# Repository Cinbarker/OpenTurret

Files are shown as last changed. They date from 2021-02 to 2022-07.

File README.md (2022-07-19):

# Open Turret
An open sourced highly accurate pan-tilt system for anything that needs to be panned and tilted!\
My goal for this project is to make a precise pan tilt mechanism that is accessible for everyone.
The hardware is still quite experimental, but I hope to refine it and release build instructions soon. Feel free to
contact me if you are interested in contributing, I will happily provide further build details.

<p float="left">
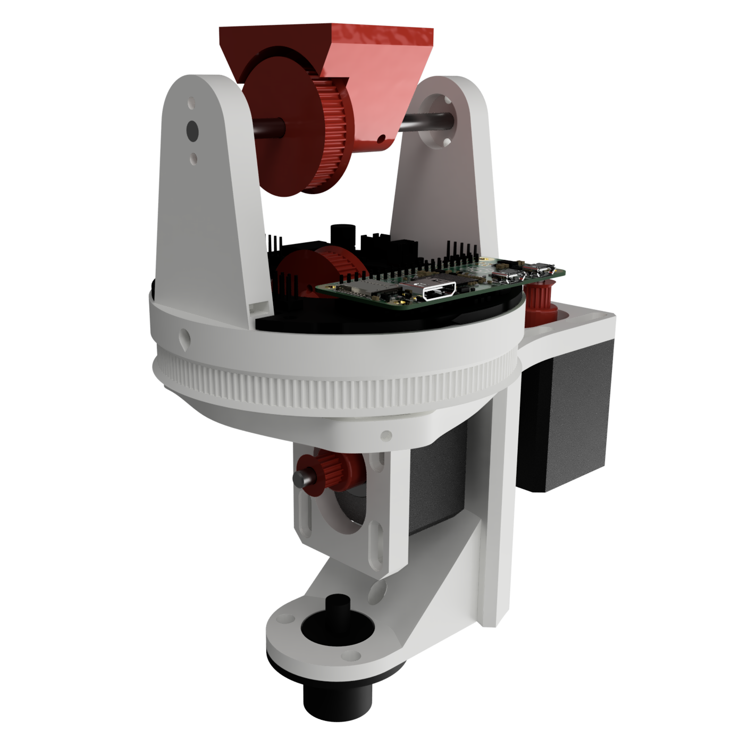
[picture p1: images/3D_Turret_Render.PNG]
3D Turret Render
  
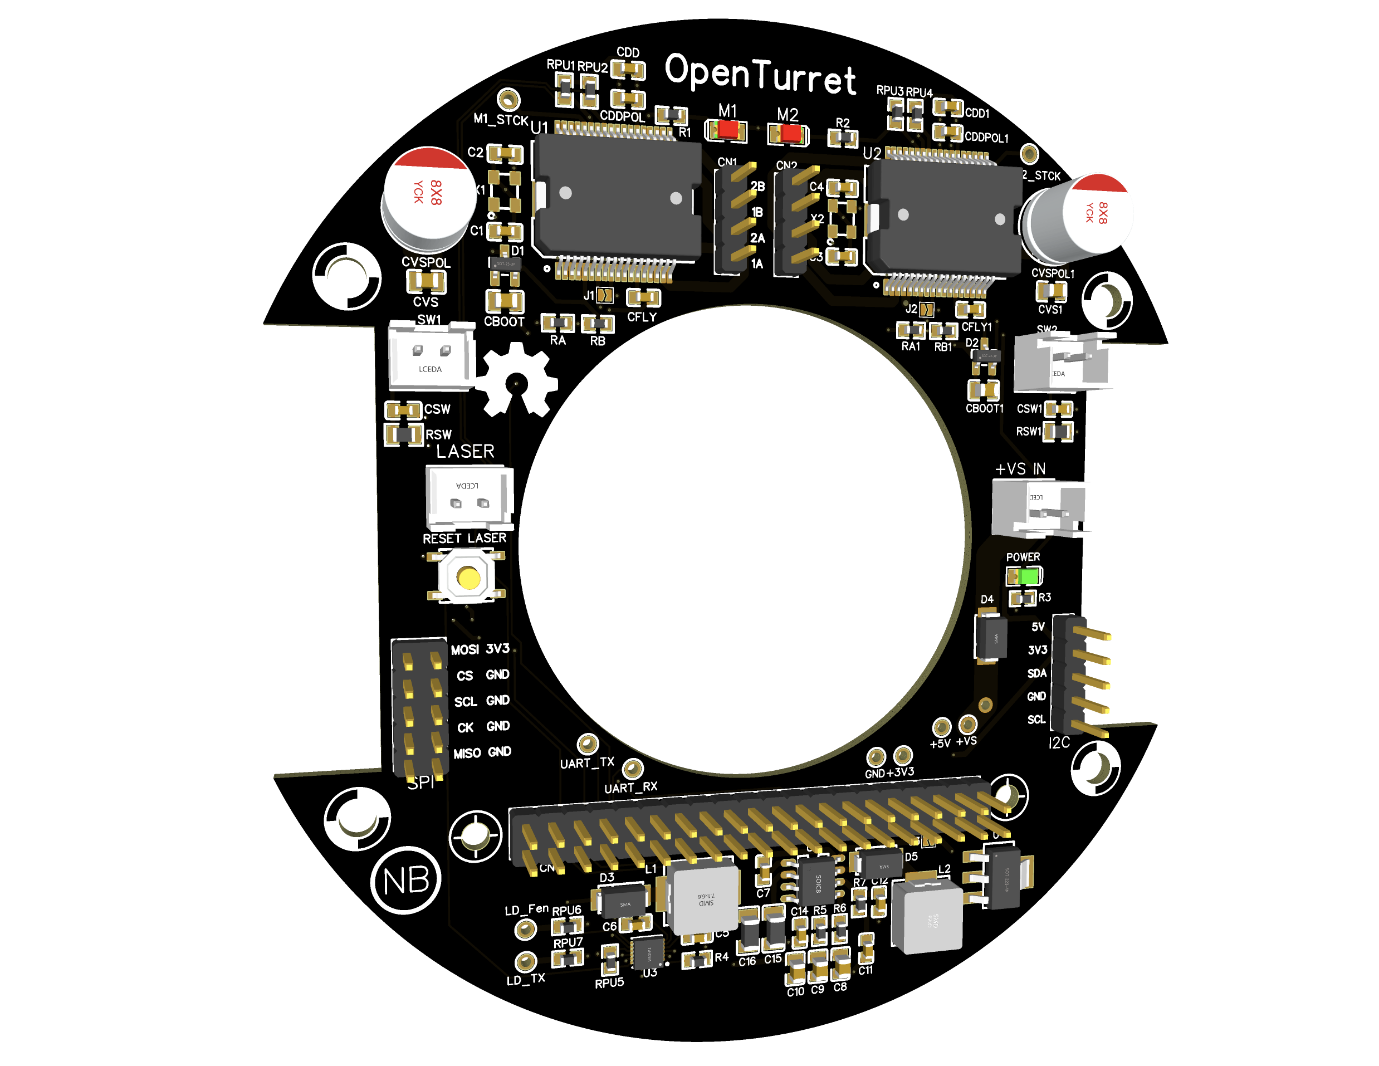
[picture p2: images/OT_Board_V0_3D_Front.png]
OpenTurret PCB 3D Front
  
</p>

### To-Do

- [ ] Hardware
  - [ ] Add holes for removing bearings from parts
  - [x] Make wiring rotation continuous (implement slipring)
  - [x] Add tripod mount
  - [x] Fix rigidity of pan axis
  - [ ] End-stops for tilt axis calibration
  - [ ] Pan Calibration Method
  - [ ] Rotary encoder on steppers for more positional feedback
  - [ ] Compass and accelerometer for positional feedback and calibration\
- [ ] PCB
  - [ ] Replace Q1 with two transistors - more accessible; less footprint specific
  - [ ] Just one oscillator for motor drivers
  - [ ] Just one ADC voltage divider
  - [ ] Correctly ground oscillator
  - [ ] SPI signal quality?
  - [ ] Buck converter noise filtering
  - [ ] Input power noise filtering (FB)
- [ ] Document Hardware
- [ ] Test load capacity and stability
  - [ ] Design large-scale version
  - [ ] Design slower much more precise version
- [x] Explore using the Pi Zero or Wireless integrate electronics below tilt axis
- [x] Get joystick to control motors
- [ ] Make easy stepper coding GUI
- [ ] Add zoom camera assembly
- [ ] Test whether the laser needs to be focussed to burn

### Code To-Do

- [ ] Add skipped step / stall error feedback
- [ ] Add tilt axis to all implementations
- [ ] Refactor I2C event methods
- [ ] Shutdown & Startup motion method
- [ ] Add config file support
  - [ ] Save settings changed in GUI to remember configs
  - [ ] Restore defaults option

### Required Specifications

- Better than 0.1º accuracy in both pan and tilt axis
- 360º continuous pan and 135º tilt in either direction
- Support weight of a laser diode
- Have a standard mounting interface
- Be as quiet and cheap as possible
- Entirely made of off-shelf or 3D printed parts
- Safety Measures
    - IR Detection
    - Radar movement detection
    - Short Pulse duration
    - Guiding laser
    - Alert before firing
    - Kill switch
- Decent speed (~36º/s)
- Targeting System
    - Manual (joystick)
    - IR Laser guided
    - Sound Guided
    - Image guided
- On-board Status Display

### Milestones

- [x]  Implement joystick control of two axes and laser
- [x]  Successfully move both axes with >=0.1º precision
- [ ]  Implement full system functionality including safety measures
- [ ]  Implement an automated detection and firing software

### Working Software Modes

- Full Manual: Control the turret and laser with a joystick
- Laser Guided: Autonomous Laser guided aiming of turret
- Sky Tracking: Use online data to track stars, planets, satellites, and air traffic. (For telescopes **NOT** lasers)

### New Software Modes Ideas

- [ ] Autonomous targeting and firing by means of image recognition
- [ ] Laser shape drawing mode
- [ ] Autonomous targeting and firing by means of acoustic triangulation

### Parts

- 2x NEMA17 Stepper Motors 0.9º 4.2 kg/cm
- 2x TMC2209 Stepper Drivers
- Joystick
- 1W Peak Laser Diode
- Bearings
- Axle Rods
- Various 3D Printed Parts
- Timing Belts
- Nuts n' Bolts

### Credit

Thank you to the following resources for making this project possible.

- Gamepad library by Piborg - https://github.com/piborg/Gamepad
- Skyfield library
- ESA, 1997, The Hipparcos and Tycho Catalogues, ESA SP-1200
- NORAD
    - CelesTrack database - https://celestrak.com/NORAD/elements/active.txt
- NAIF SPICE kernel 'de440s.bsp'
- The OpenSky Network, http://www.opensky-network.org

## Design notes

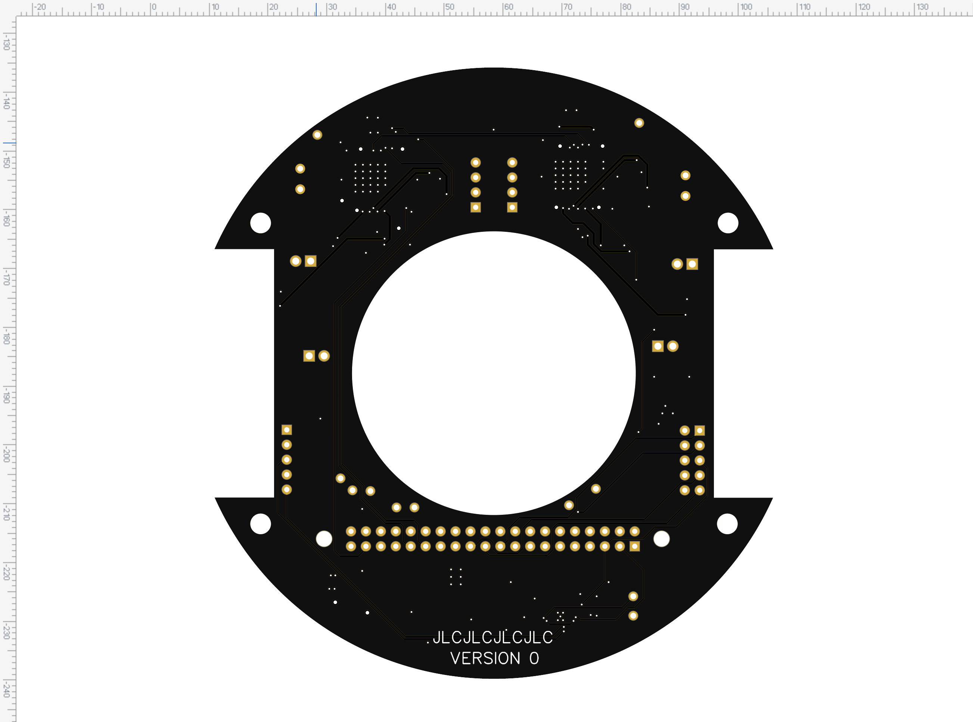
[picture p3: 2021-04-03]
images/OT_Board_V0_2D_Back.png

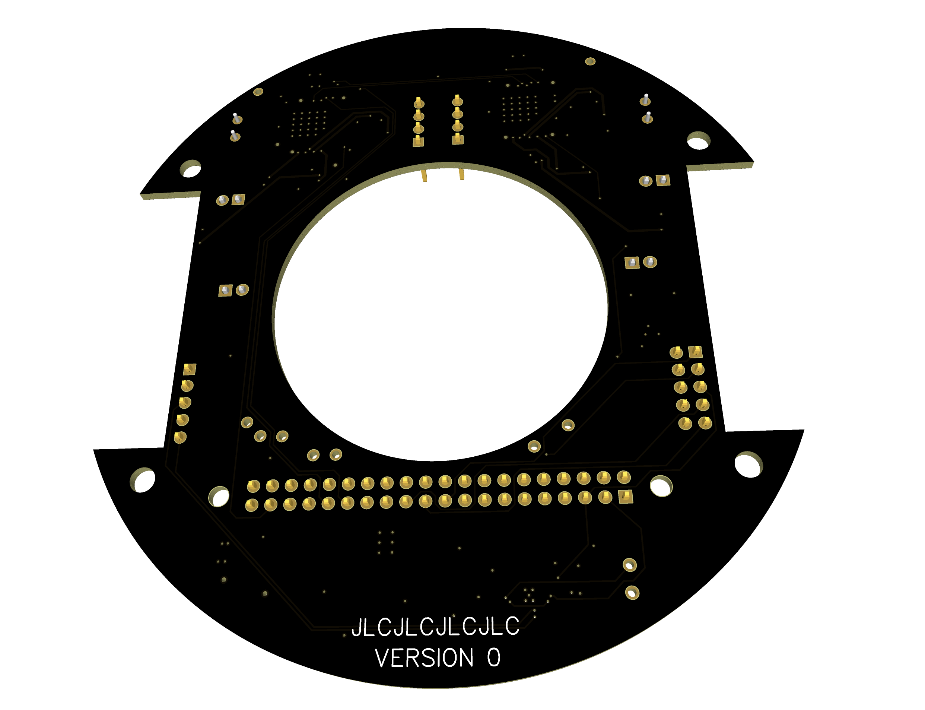
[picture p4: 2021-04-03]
images/OT_Board_V0_3D_Back.png

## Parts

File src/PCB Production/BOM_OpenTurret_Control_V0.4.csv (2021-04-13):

ID | Name | Designator | Footprint | Quantity | Manufacturer Part | Manufacturer | Supplier | Supplier Part | Price | JLCPCB SMD | LCSC Assembly | Paste Type
1 | 22pF | C1,C2,C3,C4 | C0603 | 4 | CL10C220JB8NNNC | SAMSUNG | LCSC | C1653 | 0.0055
2 | 10uF | C5,C6,CDDPOL,CDDPOL1 | C0603 | 4 | CL10A106KP8NNNC | SAMSUNG | LCSC | C19702 | 0.009 | Yes | Yes | base
3 | 22uF | C8,C9,C10 | C0805 | 3 | CL21A226MAQNNNE | SAMSUNG | LCSC | C45783 | 0.0331 |  | Yes
4 | 1nF | C11 | C0603 | 1 | CL10B102KB8NNNC | SAMSUNG | LCSC | C1588 | 0.0036 |  | Yes
5 | 10pF | C12 | C0603 | 1 | CL10C100JB8NNNC | SAMSUNG | LCSC | C1634 | 0.0046 |  | Yes
6 | 10uF | C15,C16 | C1206 | 2 | CL31A106KBHNNNE | SAMSUNG | LCSC | C13585 | 0.0437 | Yes | Yes | base
7 | 220nF | CBOOT,CBOOT1,CVS,CVS1 | C0805 | 4 | CL21B224KBFNNNE | SAMSUNG | LCSC | C5378 | 0.0152 | Yes | Yes | base
8 | 100nF | C7,CDD,CDD1 | C0603 | 3 | CC0603KRX7R9BB104 | YAGEO | LCSC | C14663 | 0.0034 | Yes | Yes | base
9 | 10nF | C14,CFLY,CFLY1,CSW,CSW1 | C0603 | 5 | 0603B103K500NT | FH | LCSC | C57112 | 0.0034 | Yes | Yes | base
10 | M1 | CN1 | HDR-M-2.54_1X4 | 1 |  |  | LCSC | C124378 | 0.0261
11 | M2 | CN2 | HDR-M-2.54_1X4 | 1 |  |  | LCSC | C124378 | 0.0261
12 | RasPi Zero (W) | CN3 | HDR-M-2.54_2X20 | 1 |  |  | LCSC | C50980 | 0.1215
13 | LASER | CN4 | CONN-TH_B2B-XH-A-LF-SN | 1 | - | JST Sales America | LCSC | C158012 | 0.0605 |  | Yes | expand
14 | +VS IN | CN5 | CONN-TH_B2B-XH-A-LF-SN | 1 | - | JST Sales America | LCSC | C158012 | 0.0605 |  | Yes | expand
15 | SW1 | CN6 | CONN-TH_B2B-XH-A-LF-SN | 1 | - | JST Sales America | LCSC | C158012 | 0.0605 |  | Yes | expand
16 | SW2 | CN7 | CONN-TH_B2B-XH-A-LF-SN | 1 | - | JST Sales America | LCSC | C158012 | 0.0605 |  | Yes | expand
17 | I2C | CN8 | HDR-M-2.54_1X5 | 1 |  |  | LCSC | C358687 | 0.0184
18 | SPI | CN9 | HDR-M-2.54_2X5 | 1 |  |  | LCSC | C178292 | 0.5019
19 | 100uF | CVSPOL,CVSPOL1 | CAP-TH_BD8.0-P3.50-D1.0-FD | 2 | 100uF 50V 8*12Black high frequency | ValuePro | LCSC | C45102 | 0.0262
20 | BAR43AFILM | D1,D2 | SOT-23-3_L2.9-W1.3-P1.90-LS2.4-BR | 2 | BAR43AFILM | STMicroelectronics | LCSC | C163327 | 0.0473
21 | SS54_C22452 | D3,D4 | SMA_L4.4-W2.8-LS5.4-R-RD | 2 | SS54 | MDD | LCSC | C22452 | 0.042 | Yes | Yes | base
22 | SS54_C22452 | D5 | SMA_L4.4-W2.8-LS5.4-R-RD | 1 | SS54 | MDD | LCSC | C22452 | 0.042 |  | Yes
23 | 2.2uH | L1 | IND-SMD_L7.3-W6.6_MHCI06030 | 1 | MCS0630-2R2MN2 | Prosperity Dielectrics | LCSC | C385252 | 0.0851 | Yes | Yes | expand
24 | 4.7uH | L2 | IND-SMD_L7.1-W6.6 | 1 | MWSA0603-4R7MT | Sunlord | LCSC | C132139 | 0.1691 |  | Yes
25 | M1 | LED1 | LED0805-R-RD | 1 | ORH-R35A | Orient | LCSC | C205444 | 0.0101 | Yes | Yes | expand
26 | M2 | LED2 | LED0805-R-RD | 1 | ORH-R35A | Orient | LCSC | C205444 | 0.0101 | Yes | Yes | expand
27 | POWER | LED3 | LED0805-R-RD | 1 | ORH-G35A | Orient | LCSC | C205442 | 0.0162 | Yes |  | recommend
28 | HSW8810 | Q1 | SOT-23-6_L2.9-W1.6-P0.95-LS2.8-BL | 1 | HSW8810 | HUASHUO | LCSC | C845594 | 0.078941
29 | 330 | R1,R2 | R0603 | 2 | 0603WAF3300T5E | UniOhm | LCSC | C23138 | 0.0012 | Yes | Yes | base
30 | 220 | R3 | R0603 | 1 | 0603WAF2200T5E | UniOhm | LCSC | C22962 | 0.0012 | Yes | Yes | base
31 | 1K | R4 | R0603 | 1 | 0603WAF1001T5E | UniOhm | LCSC | C21190 | 0.001 | Yes | Yes | base
32 | 1.96K | R5 | R0603 | 1 | 0603WAF1961T5E | UniOhm | LCSC | C22854 | 0.0011 |  | Yes
33 | 10.2K | R6 | R0603 | 1 | 0603WAF1022T5E | UniOhm | LCSC | C22772 | 0.0012 |  | Yes
34 | 68K | R7 | R0603 | 1 | 0603WAF6802T5E | UniOhm | LCSC | C23231 | 0.0014 |  | Yes
35 | 4.7K | RA,RA1 | R0603 | 2 | 0603WAF4701T5E | UniOhm | LCSC | C23162 | 0.0012 | Yes | Yes | base
36 | 62K | RB,RB1 | R0603 | 2 | 0603WAF6202T5E | UniOhm | LCSC | C23221 | 0.0011 | Yes | Yes | base
37 | 39K | RPU1,RPU2,RPU3,RPU4,RPU5,RPU6,RPU7,RPU8 | R0603 | 8 | 0603WAF3902T5E | UniOhm | LCSC | C23153 | 0.0012 | Yes | Yes | base
38 | 100 | RSW,RSW1 | R0805 | 2 | 0805W8F1000T5E | UniOhm | LCSC | C17408 | 0.0022 | Yes | Yes | base
39 | RESET LASER | SW1 | SW-SMD_4P-L5.1-W5.1-P3.70-LS6.4 | 1 | TS-1187A-B-A-B | XKB Enterprise | LCSC | C318884 | 0.021 |  | Yes
40 | POWER | SW2 | SW-SMD_4P-L5.1-W5.1-P3.70-LS6.4 | 1 | TS-1187A-B-A-B | XKB Enterprise | LCSC | C318884 | 0.021 |  | Yes
41 | L6470PD | U1,U2 | POWERSO-36_L16.0-W14.5-P0.65-LS14.5-BL-EP | 2 | L6470PD | STMicroelectronics | LCSC | C94047 | 5.9761
42 | LM3553 | U3 | WSON12(3X3) | 1 | LM3553SD/NOPB | Texas Instruments
43 | AMS1117-3.3_C347222 | U4 | SOT-223_L6.7-W3.5-P2.30-BR | 1 | AMS1117-3.3 | Youtai Semiconductor Co., Ltd. | LCSC | C347222 | 0.0366 | Yes | Yes | expand
44 | TPS54331DR | U5 | SOIC-8_L5.0-W4.0-P1.27-LS6.0-BL | 1 | TPS54331DR | TI | LCSC | C9865 | 0.2197 |  | Yes
45 | TSX-3225 16.0000MF18X-AC3 | X1,X2 | X4-SMD-3.2X2.5X0.7MM | 2 | X322516MLB4SI | YXC | LCSC | C13738 | 0.093

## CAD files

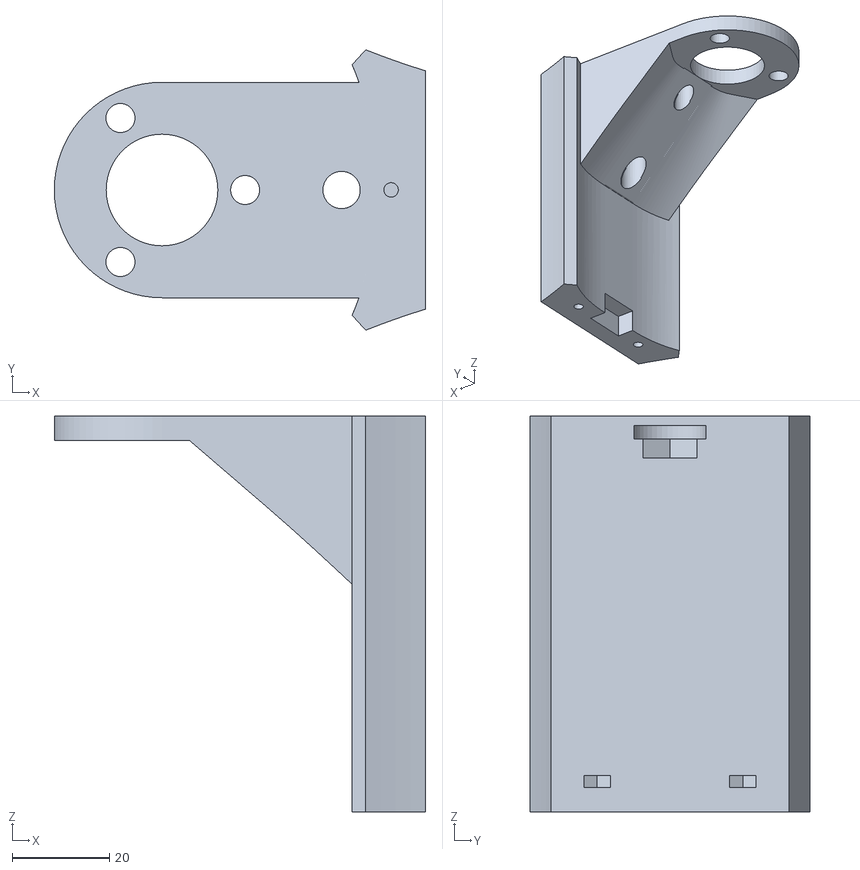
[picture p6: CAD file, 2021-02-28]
src/3D_Files/Initial Tests/Tripod mount V0.stl
76.5 x 57.8 x 81.6

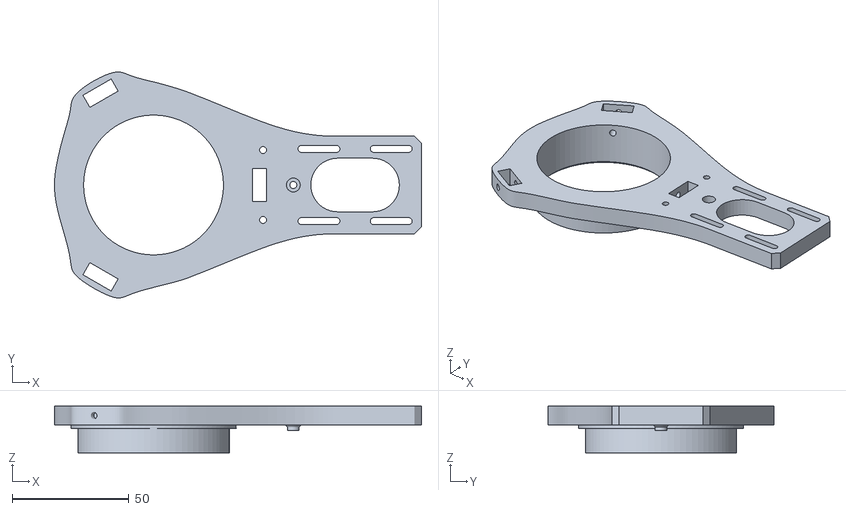
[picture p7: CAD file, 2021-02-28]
src/3D_Files/Initial Tests/Pan Fixture V2 Print.stl
157.5 x 97.0 x 20.0

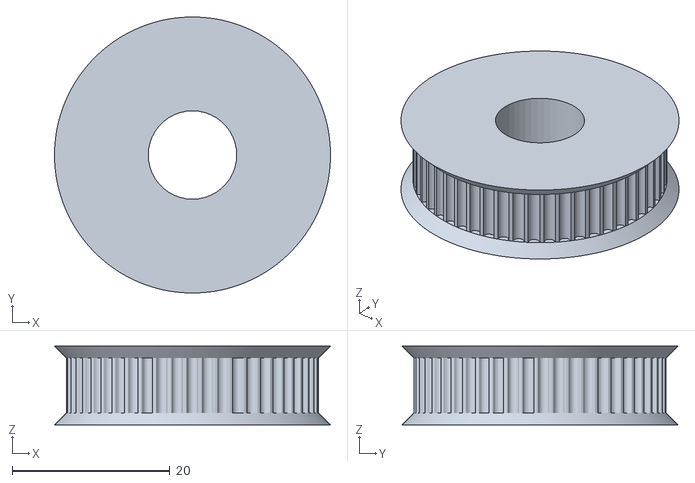
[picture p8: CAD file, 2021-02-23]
src/3D_Files/Initial Tests/51_Tooth_hub_11.2_bore.stl
35.0 x 35.0 x 10.0

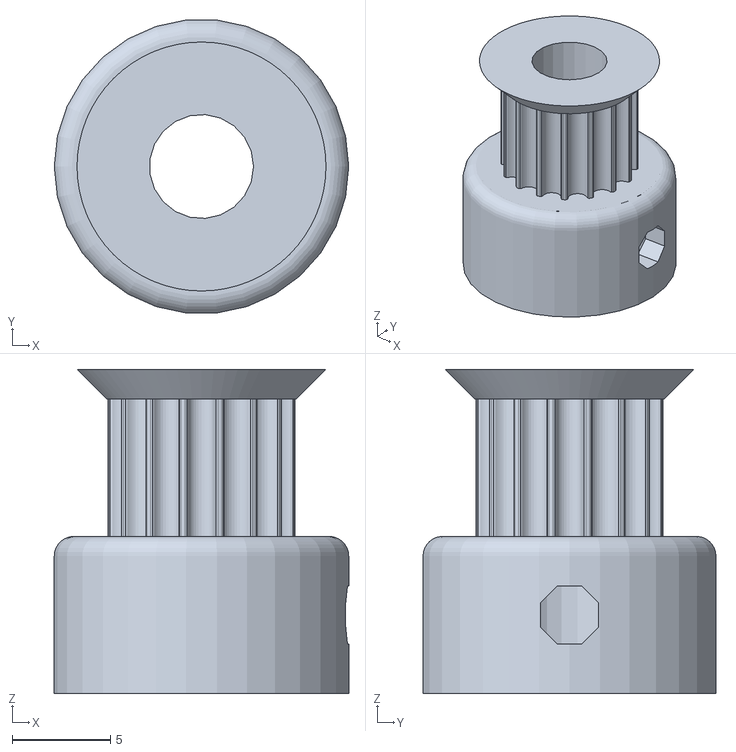
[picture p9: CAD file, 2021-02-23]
src/3D_Files/Initial Tests/16_Tooth_pulley.stl
15.0 x 14.9 x 16.5

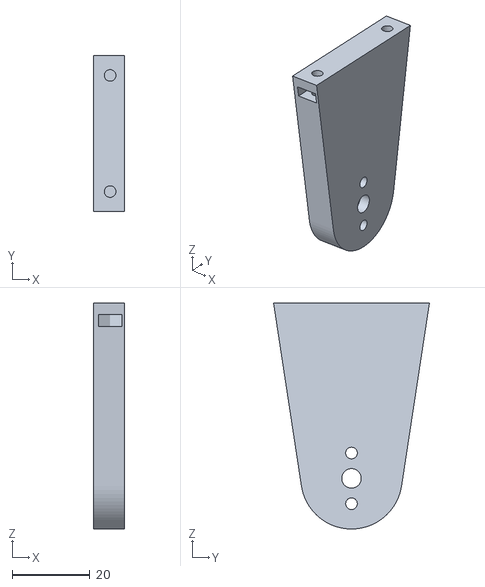
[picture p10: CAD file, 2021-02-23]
src/3D_Files/Initial Tests/Tilt Support V2.stl
8.00 x 40.0 x 58.0

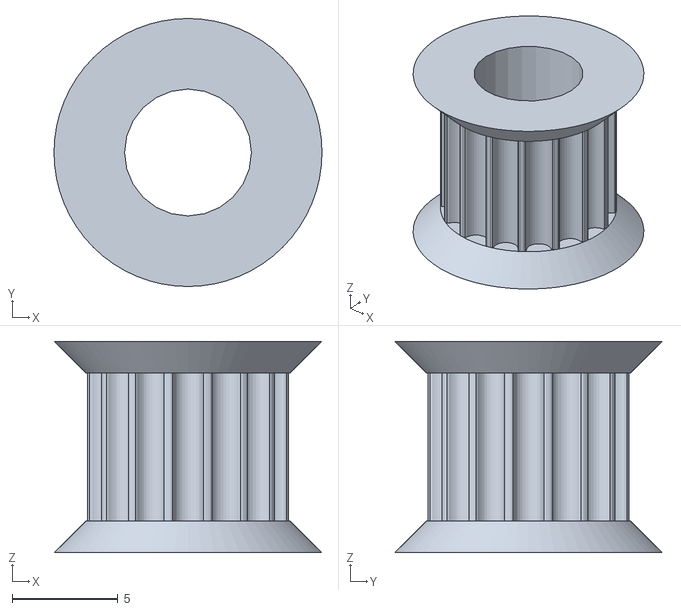
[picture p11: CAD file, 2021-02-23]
src/3D_Files/Initial Tests/16_Tooth_hub_6_bore.stl
12.7 x 12.7 x 10.0

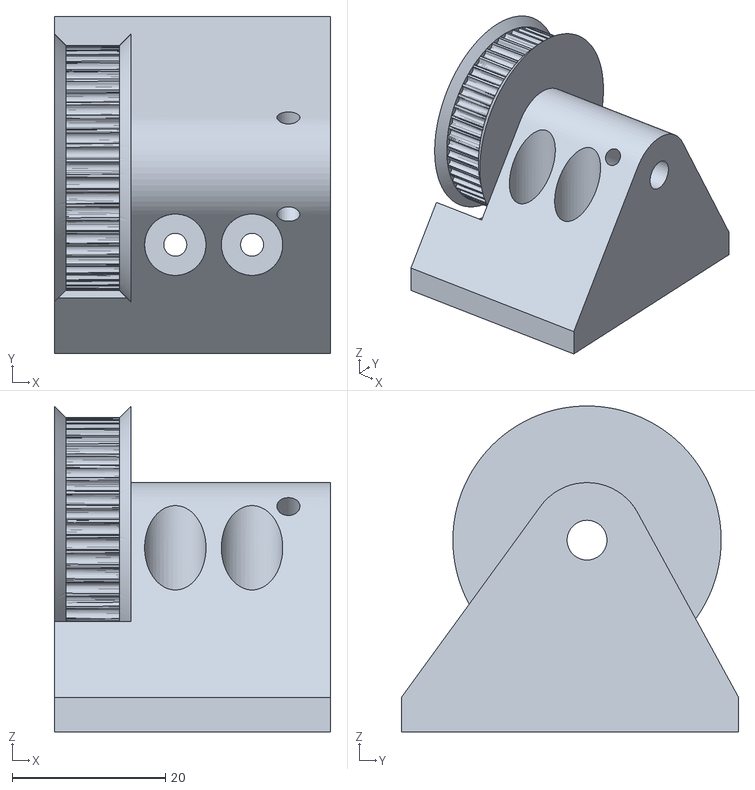
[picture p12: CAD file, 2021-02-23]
src/3D_Files/Initial Tests/Tilt Floor.stl
36.0 x 44.0 x 42.5

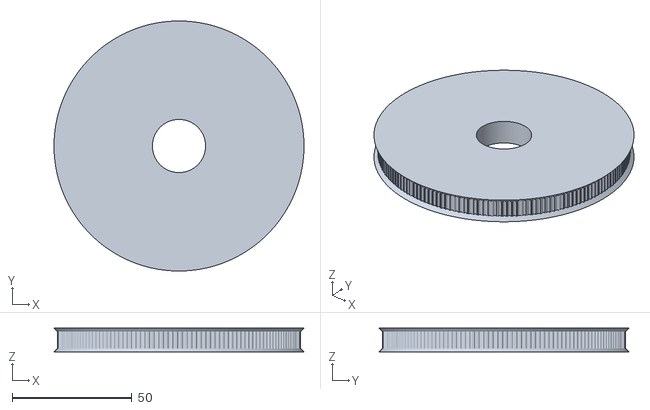
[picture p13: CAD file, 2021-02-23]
src/3D_Files/Initial Tests/Raw GT2 160 tooth hub.stl
104.4 x 104.4 x 10.0

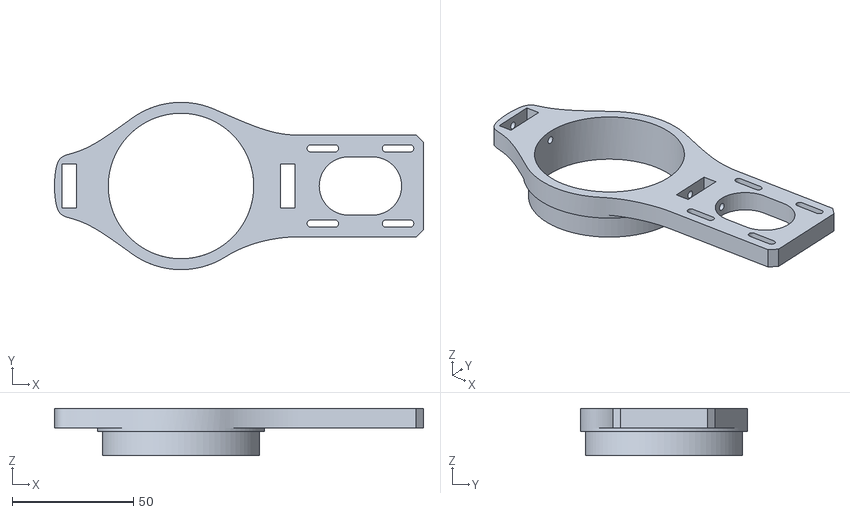
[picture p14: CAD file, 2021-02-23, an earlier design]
src/3D_Files/Initial Tests/Pan Fixture V0 Print.stl
152.2 x 69.0 x 19.5

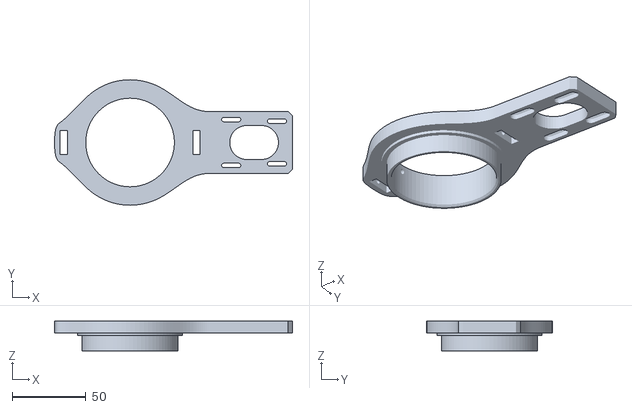
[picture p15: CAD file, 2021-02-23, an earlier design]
src/3D_Files/Initial Tests/Pan Fixture V1 Print.stl
161.2 x 85.0 x 20.0

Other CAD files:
src/3D_Files/Initial Tests/Tilt Support V1.stl

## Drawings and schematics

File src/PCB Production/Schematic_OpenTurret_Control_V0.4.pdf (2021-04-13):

## MOTOR 1 CONTROL

## RASPBERRY PI

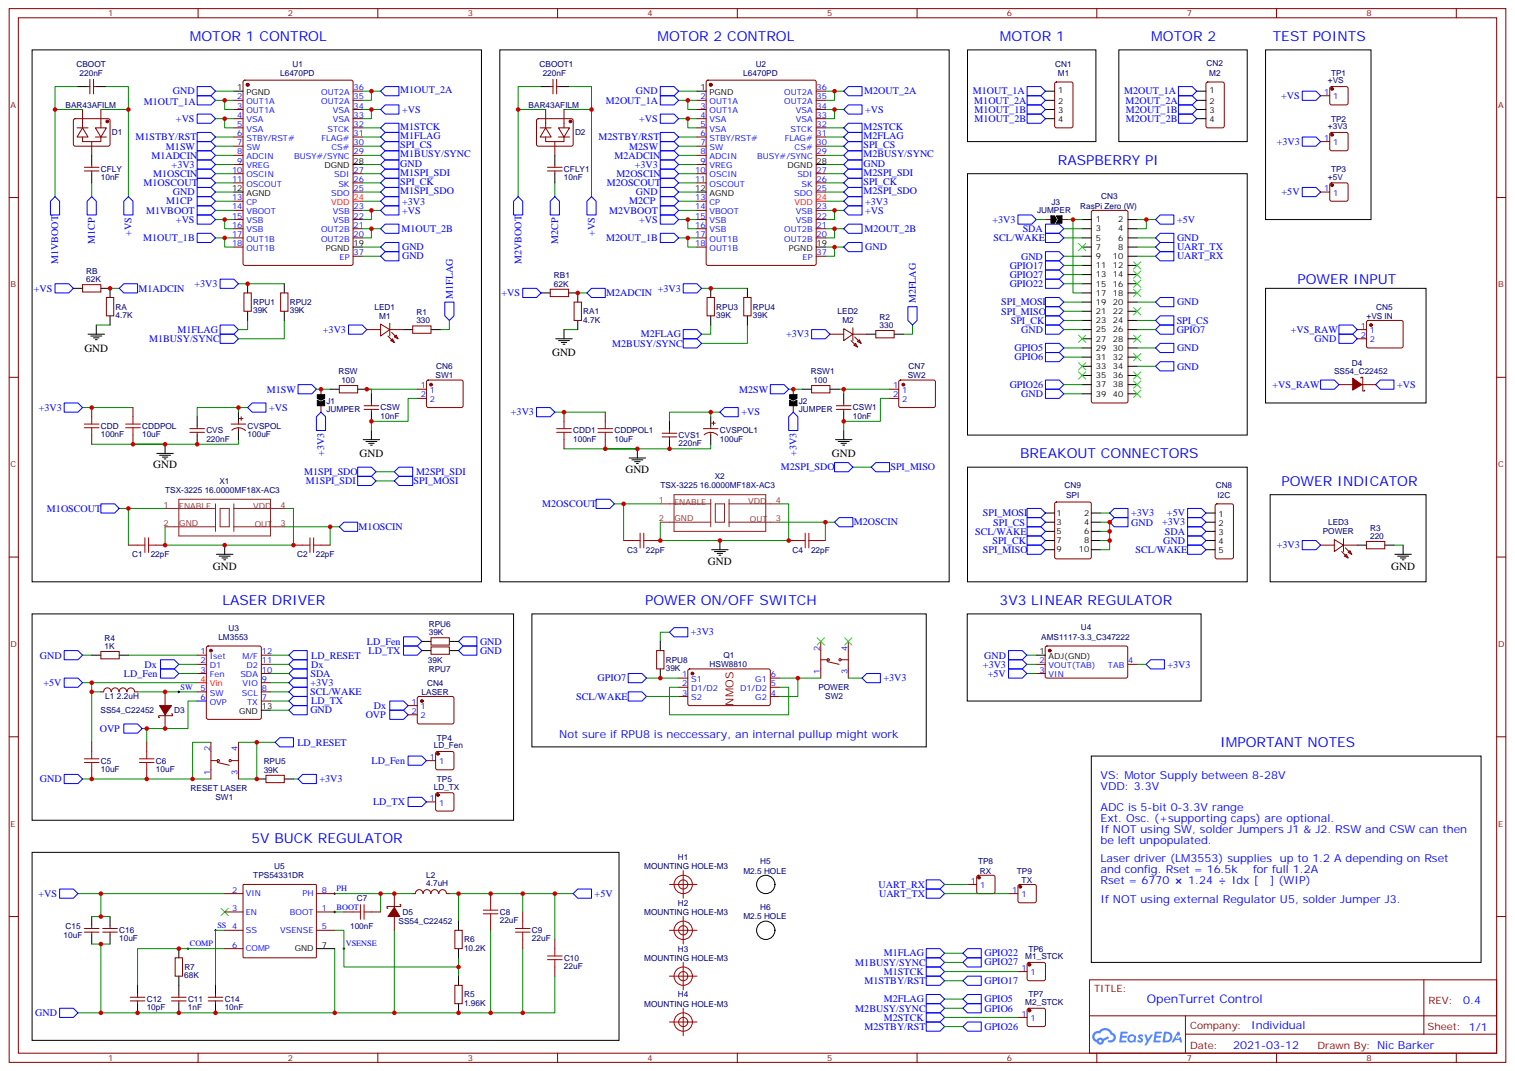
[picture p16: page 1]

POWER ON/OFF SWITCH

Not sure if RPU8 is neccessary, an internal pullup might work

VS: Motor Supply between 8-28V
VDD: 3.3V
ADC is 5-bit 0-3.3V range
Ext. Osc. (+supporting caps) are optional.
If NOT using SW, solder Jumpers J1 & J2. RSW and CSW can then
be left unpopulated.
Laser driver (LM3553) supplies up to 1.2 A depending on Rset
and config. Rset = 16.5k for full 1.2A
If NOT using external Regulator U5, solder Jumper J3.

Drawn By: Nic Barker

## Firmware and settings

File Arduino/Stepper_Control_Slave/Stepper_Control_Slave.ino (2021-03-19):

/*
 * This sketch was designed for Arduino Unos to ask as a real time slave of a Raspberry Pi. 
 * If using another board, the things that must mbe changed are:
 *    - SDA and SCL pins for I2C bus (this is a hardware change, check Wire library for more info)
 *    - PORT registers will most likely be different. For more info: https://www.arduino.cc/en/Reference/PortManipulation
 */


#include <Wire.h>

// Define constants
#define address 0x8 // I2C address of this slave device
#define panStepPin 4 //B00010000 // Pin D4
#define panDirPin B00100000 // Pin D5
#define tiltStepPin 6 //B01000000 // Pin D6
#define tiltDirPin B10000000 // Pin D7
#define laserPin 9 //B00000100 // Pin D9

// Initialize variables
byte data[8];
byte panSpeed = 0, tiltSpeed = 0, panDir = 0, tiltDir = 0, calibrate = 0, laserPower = 0, laserFire = 0, returnHome = 0, dPadX = 1, dPadY = 1;

// Configure stepper motor speed limits (lower minDelay => higher maxSpeed)
int minDelay = 40;
int maxDelay = 300;
int scale = 3;

//
long minTilt = -1800 * 16;
long maxTilt = 2000 * 16;

long panLocation = 0, tiltLocation = 0;

byte currentPanDir = 0, currentTiltDir = 0;

unsigned long currentPanMicros = 0;
unsigned long previousPanMicros = 0;
unsigned long currentTiltMicros = 0;
unsigned long previousTiltMicros = 0;

byte panState = 0, tiltState = 0;
int panDelay = 0, tiltDelay = 0;


void setup() {
  Serial.begin(9600);
  pinMode(A5, OUTPUT);
  digitalWrite(A5, LOW);
  // Set in/out mode of pins
  pinMode(panStepPin, OUTPUT);
  pinMode(panDirPin, OUTPUT);
  pinMode(tiltStepPin, OUTPUT);
  pinMode(tiltDirPin, OUTPUT);
  pinMode(laserPin, OUTPUT);

  Wire.begin(address);
  Wire.onReceive(receiveEvent); // Declared in setup() to receive data from Master
}

void loop() {

  if (laserFire == 1) {
    //PORTB |= laserPort;
    digitalWrite(laserPin, HIGH);
    delay(10);
    //PORTB &= !laserPort;
    digitalWrite(laserPin, LOW);
    laserFire = 0;
  } else {
    analogWrite(laserPin, laserPower/4);
  }

  ///// Control Pan Mechanism /////

  if (panSpeed != 0) {
    if (panDir == 1) PORTD |= panDirPin;
    else PORTD &= !panDirPin;
    stepMotor(panStepPin, panDelay, &currentPanMicros, &previousPanMicros, &panState, panDir, &panLocation);
  }

  // Reset 128000 is one full rotation
  if (abs(panLocation / 128000) == 1) {
    panLocation = 0;
  }

  ///// Control Tilt Mechanism /////

  if ((tiltSpeed != 0) && ((tiltLocation >= minTilt) || (tiltDir == 0)) && ((tiltLocation <= maxTilt) || (tiltDir == 1))) {
    if (tiltDir == 1) PORTD &= !tiltDirPin;
    else PORTD |= tiltDirPin;
    stepMotor(tiltStepPin, tiltDelay, &currentTiltMicros, &previousTiltMicros, &tiltState, tiltDir, &tiltLocation);
  }
}

// Function for stepping the motor without incurring delays in the main loop
void stepMotor(int pin, int delayTime, long* currentMicros, long* previousMicros, byte* state, byte dir, long* location) {
  *currentMicros = micros();
  if (*currentMicros - *previousMicros >= delayTime) {
    *previousMicros = *currentMicros;
    if (*state == LOW) {
      *state = HIGH;
    } else {
      *state = LOW;
    }
    digitalWrite(pin, *state);
    if (dir == 0) *location = *location + 1;
    else *location = *location - 1;
  }
}

// Function for receiving I2C data
// Data Structure: dataArray[panSpeed, tiltSpeed, panDir, tiltDir, calibrate, laserPower, laserFire, returnHome, dPadX, dPadY]
void receiveEvent(int howmany) { //howmany = Wire.write() executed by Master
  for (int i = 0; i < howmany; i++) {
    data[i] = Wire.read();
    //Serial.println(dataArray[i], DEC);
  }
  panSpeed   = data[1];
  tiltSpeed  = data[2];
  panDir     = data[3];
  tiltDir    = data[4];
  calibrate  = data[5];
  laserPower = data[6];
  laserFire  = data[7];
  returnHome = data[8];
  dPadX      = data[9];  // 0:Left 1:Mid  2:Right
  dPadY      = data[10]; // 0:Low  1:Mid  2:High

  if (dPadY == 0) { scale = 15; }
  else if (dPadY == 1) { scale = 3; }
  else if (dPadY == 2) { scale = 1; }
  
  panDelay = map(panSpeed, 0, 255, scale*maxDelay, scale*minDelay);
  tiltDelay = map(tiltSpeed, 0, 255, scale*maxDelay, scale*minDelay);
  // Calibrate loactions
  if (calibrate == 1) {
    panLocation = 0;
    tiltLocation = 0;
    calibrate = 0;
  }
  // Indvidual stepping of pan axis
  if (dPadX == 0) {
    PORTD &= !panDirPin;
    panDelay = 80;
    for (int i = 0; i<20-scale; i++){
      digitalWrite(panStepPin, !panState);
      panLocation++;
      delayMicroseconds(panDelay);
      digitalWrite(panStepPin, panState);
      panLocation++;
      delayMicroseconds(panDelay);
    }
    Serial.println(dPadX, DEC);
    dPadX = 1;
  } else if (dPadX == 2){
    PORTD |= panDirPin;
    panDelay = 80;
    for (int i = 0; i<20-scale; i++){
      digitalWrite(panStepPin, !panState);
      panLocation--;
      delayMicroseconds(panDelay);
      digitalWrite(panStepPin, panState);
      panLocation--;
      delayMicroseconds(panDelay);
    }
    Serial.println(dPadX, DEC);
    dPadX = 1;
  }

  // Return to home
  if (returnHome==1){
    panDelay = 80;
    if (panLocation < 0) {
      PORTD &= !panDirPin;
      panLocation *= -1;
    } else {
      PORTD |= panDirPin;
    }
    while (panLocation > 0) {
      digitalWrite(panStepPin, !panState);
      panLocation--;
      delayMicroseconds(panDelay);
      digitalWrite(panStepPin, panState);
      panLocation--;
      delayMicroseconds(panDelay);
    }
    returnHome = 0;
  }
  
//   PORTD &= !panDirPin;
//   panDelay = minDelay;
//   
//    for (int i = 0; i<20-scale; i++){
//      digitalWrite(panStepPin, !panState);
//      delayMicroseconds(minDelay);
//      panLocation++;
//      digitalWrite(panStepPin, panState);
//      delayMicroseconds(minDelay);
//      panLocation++;
//    }
  Serial.print(panLocation, DEC);
  Serial.print("\t");
  Serial.println(dPadY, DEC);
  
}

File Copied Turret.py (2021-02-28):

try:
    import cv2
except Exception as e:
    print("Warning: OpenCV not installed. To use motion detection, make sure you've properly configured OpenCV.")

import time
import thread
import threading
import atexit
import sys
import termios
import contextlib

import imutils
import RPi.GPIO as GPIO
from Adafruit_MotorHAT import Adafruit_MotorHAT, Adafruit_DCMotor, Adafruit_StepperMotor


### User Parameters ###

MOTOR_X_REVERSED = False
MOTOR_Y_REVERSED = False

MAX_STEPS_X = 30
MAX_STEPS_Y = 15

RELAY_PIN = 22

#######################


@contextlib.contextmanager
def raw_mode(file):
    """
    Magic function that allows key presses.
    :param file:
    :return:
    """
    old_attrs = termios.tcgetattr(file.fileno())
    new_attrs = old_attrs[:]
    new_attrs[3] = new_attrs[3] & ~(termios.ECHO | termios.ICANON)
    try:
        termios.tcsetattr(file.fileno(), termios.TCSADRAIN, new_attrs)
        yield
    finally:
        termios.tcsetattr(file.fileno(), termios.TCSADRAIN, old_attrs)


class VideoUtils(object):
    """
    Helper functions for video utilities.
    """
    @staticmethod
    def live_video(camera_port=0):
        """
        Opens a window with live video.
        :param camera:
        :return:
        """

        video_capture = cv2.VideoCapture(camera_port)

        while True:
            # Capture frame-by-frame
            ret, frame = video_capture.read()

            # Display the resulting frame
            cv2.imshow('Video', frame)

            if cv2.waitKey(1) & 0xFF == ord('q'):
                break

        # When everything is done, release the capture
        video_capture.release()
        cv2.destroyAllWindows()

    @staticmethod
    def find_motion(callback, camera_port=0, show_video=False):

        camera = cv2.VideoCapture(camera_port)
        time.sleep(0.25)

        # initialize the first frame in the video stream
        firstFrame = None
        tempFrame = None
        count = 0

        # loop over the frames of the video
        while True:
            # grab the current frame and initialize the occupied/unoccupied
            # text

            (grabbed, frame) = camera.read()

            # if the frame could not be grabbed, then we have reached the end
            # of the video
            if not grabbed:
                break

            # resize the frame, convert it to grayscale, and blur it
            frame = imutils.resize(frame, width=500)
            gray = cv2.cvtColor(frame, cv2.COLOR_BGR2GRAY)
            gray = cv2.GaussianBlur(gray, (21, 21), 0)

            # if the first frame is None, initialize it
            if firstFrame is None:
                print "Waiting for video to adjust..."
                if tempFrame is None:
                    tempFrame = gray
                    continue
                else:
                    delta = cv2.absdiff(tempFrame, gray)
                    tempFrame = gray
                    tst = cv2.threshold(delta, 5, 255, cv2.THRESH_BINARY)[1]
                    tst = cv2.dilate(tst, None, iterations=2)
                    if count > 30:
                        print "Done.\n Waiting for motion."
                        if not cv2.countNonZero(tst) > 0:
                            firstFrame = gray
                        else:
                            continue
                    else:
                        count += 1
                        continue

            # compute the absolute difference between the current frame and
            # first frame
            frameDelta = cv2.absdiff(firstFrame, gray)
            thresh = cv2.threshold(frameDelta, 25, 255, cv2.THRESH_BINARY)[1]

            # dilate the thresholded image to fill in holes, then find contours
            # on thresholded image
            thresh = cv2.dilate(thresh, None, iterations=2)
            c = VideoUtils.get_best_contour(thresh.copy(), 5000)

            if c is not None:
                # compute the bounding box for the contour, draw it on the frame,
                # and update the text
                (x, y, w, h) = cv2.boundingRect(c)
                cv2.rectangle(frame, (x, y), (x + w, y + h), (0, 255, 0), 2)
                callback(c, frame)

            # show the frame and record if the user presses a key
            if show_video:
                cv2.imshow("Security Feed", frame)
                key = cv2.waitKey(1) & 0xFF

                # if the `q` key is pressed, break from the lop
                if key == ord("q"):
                    break

        # cleanup the camera and close any open windows
        camera.release()
        cv2.destroyAllWindows()

    @staticmethod
    def get_best_contour(imgmask, threshold):
        im, contours, hierarchy = cv2.findContours(imgmask, cv2.RETR_EXTERNAL, cv2.CHAIN_APPROX_SIMPLE)
        best_area = threshold
        best_cnt = None
        for cnt in contours:
            area = cv2.contourArea(cnt)
            if area > best_area:
                best_area = area
                best_cnt = cnt
        return best_cnt
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

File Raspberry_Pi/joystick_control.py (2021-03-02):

#!/usr/bin/env python
# coding: utf-8
# This file is the main operating one

# Load  libraries
import Gamepad
import time
import atexit
from gpiozero import PWMOutputDevice

# Import local files
from turret_i2c import I2cData
from turret_gamepad import TMJoystick

# Define GPIO output pins
laserOutput = PWMOutputDevice(18, True, 0, 1000, None)

# Create instance of i2c_data class
i2cd = I2cData(0x8)

# Gamepad settings
gamepad_type = TMJoystick
button_trigger = 'TRIGGER'
button_center = 'CENTER'
button_exit = 'BACK'
button_RTH = 'RIGHT'
joystick_pan = 'JOY-X'
joystick_tilt = 'JOY-Y'
slider_power = 'SLIDER'
dpad_x = 'DPAD-X'
dpad_y = 'DPAD-Y'

pollInterval = 0.1

# Wait for a connection
if not Gamepad.available():
    print('Please connect your gamepad...')
    while not Gamepad.available():
        time.sleep(1.0)
gamepad = gamepad_type()
print('Gamepad connected')

# Set initial states
laser_power = 0
running = True
center_on = False


# Create callback functions
def trigger_button_pressed():
    i2cd.set_laser_on(1)
    i2cd.send_data()
    i2cd.set_laser_on(0)
    print('fired')

def trigger_button_released():
    pass


def center_button_pressed():
    i2cd.set_calibrate(1)
    i2cd.send_data()
    i2cd.set_calibrate(0)
    print("CALIBRATED")


def exit_button_pressed():
    global running
    i2cd.reset()
    print('\033[1;31;40m EXIT! \033[1;37;40m')
    running = False


def rth_button_pressed():
    i2cd.set_return_to_home(1)
    i2cd.send_data()
    i2cd.set_return_to_home(0)


def pan_axis_moved(pan_speed):
    i2cd.set_pan_dir(0 if pan_speed < 0 else 1)
    i2cd.set_pan_speed(abs(int(pan_speed * 255)))
    i2cd.send_data()
    print('Pan: ' + str(round(pan_speed, 3)))


def tilt_axis_moved(tilt_speed):
    i2cd.set_tilt_dir(0 if tilt_speed < 0 else 1)
    i2cd.set_tilt_speed(abs(int(tilt_speed * 255)))
    print('Tilt: ' + str(round(tilt_speed, 3)))
    i2cd.send_data()


def power_axis_moved(laser):
    global laser_power
    laser_power = int((-laser + 1) * 255 / 2)
    i2cd.set_laser_power(laser_power)
    i2cd.send_data()
    print('Laser _power: ' + str(round(laser_power, 3)))


def dpad_x_axis_moved(pad_x):
    if pad_x == 1:
        output = 2
        dir_x = 'RIGHT'
    elif pad_x == -1:
        output = 0
        dir_x = 'LEFT'
    else:
        output = 1
        dir_x = 'MID'
    i2cd.set_dpad_x(output)
    i2cd.send_data()
    i2cd.set_dpad_x(1)
    print('dPad-X: ' + dir_x)


def dpad_y_axis_moved(pad_y):
    if pad_y == 1:
        output = 0
        dir_y = 'DOWN'
    elif pad_y == -1:
        output = 2
        dir_y = 'UP'
    else:
        output = 1
        dir_y = 'MID'
    i2cd.set_dpad_y(output)
    i2cd.send_data()
    print('dPad-Y: ' + dir_y)


# Start the background updating
gamepad.startBackgroundUpdates()

# Register the callback functions
gamepad.addButtonPressedHandler(button_trigger, trigger_button_pressed)
gamepad.addButtonReleasedHandler(button_trigger, trigger_button_released)
gamepad.addButtonPressedHandler(button_center, center_button_pressed)
gamepad.addButtonPressedHandler(button_exit, exit_button_pressed)
gamepad.addButtonPressedHandler(button_RTH, rth_button_pressed)
gamepad.addAxisMovedHandler(joystick_pan, pan_axis_moved)
gamepad.addAxisMovedHandler(joystick_tilt, tilt_axis_moved)
gamepad.addAxisMovedHandler(slider_power, power_axis_moved)
gamepad.addAxisMovedHandler(dpad_x, dpad_x_axis_moved)
gamepad.addAxisMovedHandler(dpad_y, dpad_y_axis_moved)


def exit_handler():
    i2cd.reset()
    print('\033[1;31;40m EXIT! \033[1;37;40m')
    
# Handle exit protocol
atexit.register(exit_handler)

# Keep running while joystick updates are handled by the callbacks
try:
    while running and gamepad.isConnected():
        # Show the current pan and tilt
        # print('%+.1f %% pan_speed, %+.1f %% tilt_speed' % (pan_speed * 100, tilt_speed * 100))
        # Sleep for our polling interval
        time.sleep(pollInterval)
finally:
    # Ensure the background thread is always terminated when we are done
    gamepad.disconnect()

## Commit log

2021-02-22 commit from Raspberry Pi
2021-02-22 fix tilt axis direction control
    [MainControl.py]
2021-02-22 add calibration protocol
2021-02-22 rename center button mapping
2021-02-23 fix delay-less motor stepping
    [Stepper_Control_Slave.ino]
2021-02-23 Sending of laser data i2c
2021-02-24 add laser support to hardware
2021-02-24 Add RTH button - i2c
2021-03-01 DPad Y axis speed modes
2021-03-01 Calibrate before sending data
2021-03-03 added pan laser control
2021-04-03 Add renders of OT Board V0
2021-04-22 Get Air Traffic data in a separate thread to avoid GUI freeze
    [OpenTurret_UI.py, PyUi.py, UITest.py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]
2022-02-15 make camera_calibration_thread.py
